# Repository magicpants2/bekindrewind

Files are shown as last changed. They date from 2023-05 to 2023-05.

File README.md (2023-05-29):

# bekindrewind
Tape measure spring powered auto rewind spool holder

Current auto rewind spools use 3d printed plastic springs to rewind the spool. Bekindrewind uses a spring from a 6ft tape that will not fatigue and fail over time like a 3d printed spring. In an effort to make the project more accesible and cheaper it uses 3d printed bearings with standard 4.5mm BBs. The current design uses only one 608 bearing. 

# How it works
The spring coils inside the mandrel and rotates around the center shaft. Sprial traces with bbs rotate and allow for a determined number of rotations. After the number of rotations the center shaft and the spool holder lock together in one direction. A torque limiter located in the end bearing will become overloaded and rotate. Allowing the entire assembly to rotate with little more resistance than the spring.

cut veilw

# BOM
1 608 bearing

1 6ft "Master mechanic" tape measure (I have not tested other brands but its the cheapest one Ive found

~ 63 4.5mm bb gun bbs

2 3mm heatset inserts

2 M3*8

1 8*15*.3 spring washer

Printed parts

# Part settings

In the interest of time I have provided a .3mf file of the assembly. This can be brought into your slicer and ungrouped. From there the parts can be oriented in the best way for strength 

Normal voron settings worked for me. 40% infill with 4 outer lines

Make sure your printer is fully tuned as there are tight tolerances on the bearings and sliding parts

The only part that requires support is the larger hexigon part on the end bearings. This must be printed so that the inner circle is facing up and not an overhang as shown below

endbearingorientation

# Assembly

expendbearing

The end bearings require the most bbs and can be tedious. It is not represented in these pictures but the guide for the outer trace of bearings needs to face the opposite direction to load from the bottom. It does take an amount of force to persuade the bbs into the traces. The assembly requires 2 of the bearing assemblies however only one needs the torque limiter installed (located inside of the large hex) 

cutortho

Start by pressing the 608 bearing into the hex in the mandrel. Winding the spring into the mandrel is dangerous and requires some finess and patience. There are some videos on youtube on how to take apart the tape measure that I suggest you reaserch on your own. I highly suggest ppe. Gloves and safety glasses are a must. I had many cuts from the spring getting loose and very nearly lost an eye. So I cannot under state how decivingly dangerous it can be. As such I am not responsible for your ill advised experements. I might make a video in the future but as of now this is a beta test

I suggest using 1 of the spiral parts (Diagram shows 3) to make for 3 rotations. To many rotations can pull the spring out of the mandrel and force you to rebuild the spring assembly

assemble the mandrel and other parts as shown on the shaft then slide the assembly into the main cylinder. Screwing the end bearing into place as it inserts

springass

Make sure everything spins freely and smoothly. I use 3 in 1 oil to lubricate all the parts that move. To set the torque limiter rotate the threaded hex until it is almost tight. Rotate the entire assembly to wind it up. It should rotate the 3 times without slipping. Loosen the nut and repeat the process until it slips when fully wound but not before. It can be a little tricky. 

I am wrapping electrical tape around the main body in order to attatch it to the spool for testing, there is currently no stand yet. 

Please keep in mind this is in beta testing and it is not yet ready for full implementation

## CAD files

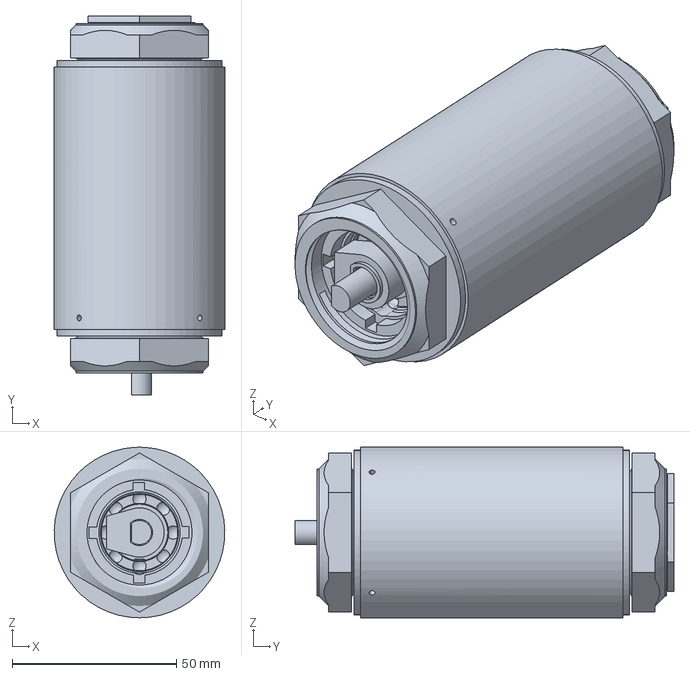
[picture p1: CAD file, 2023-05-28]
internal_buffer.3MF
52.0 x 115.5 x 52.0 mm
